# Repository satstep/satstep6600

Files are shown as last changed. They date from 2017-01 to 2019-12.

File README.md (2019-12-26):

<h1 style="font-family: courier;" align="center"> satstep6600</h1>
<p align="center">
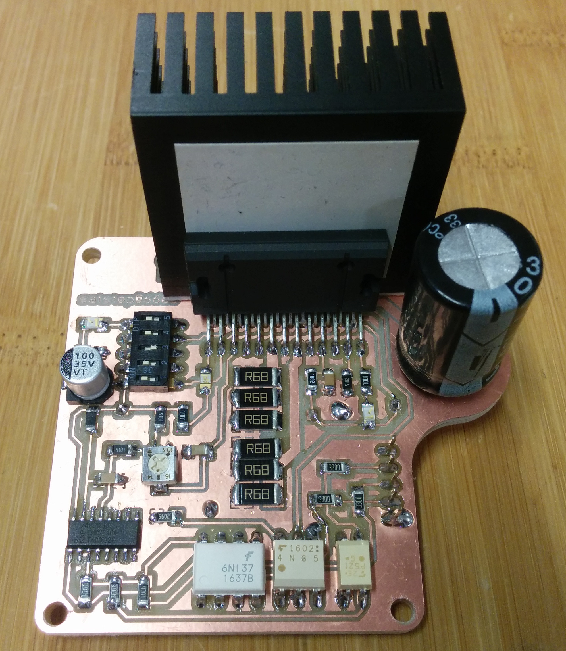
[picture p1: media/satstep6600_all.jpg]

<div align="center"><i>An open source & fabbable stepper driver based on TB6600.</i></div>
</p>

satstep6600
--

satstep6600 is a **low cost and fabbable** stepper driver. Inspired by the [PiBot TB6600 stepper driver](http://reprap.org/wiki/PiBot_TB6600_Stepper_Driver), satstep6600 is designed on purpose to maintain all the high power specs while being safe to be operated and easy to build, even using the stardard Fab Lab equipment.

satstep6600 features:

- chopper type stepper motor driver
- 5A peak output current, **4.5A** sustained maximum (over 2A a fan is recommended)
- 8-40V input voltage 
- 1/1, 1/2A(0-71-100%), 1/2B(0-100%), 1/4, 1/8, 1/16 stepping modes
- suitable for NEMA 17, NEMA 23 and few NEMA 34 stepper motors
- thermal shut down protection
- under voltage lock out protection
- over-current detection protection
- optoisolated for all the inputs
- 4 x M3 fixing holes
- board size of 70x63mm
- it costs **13 euro**

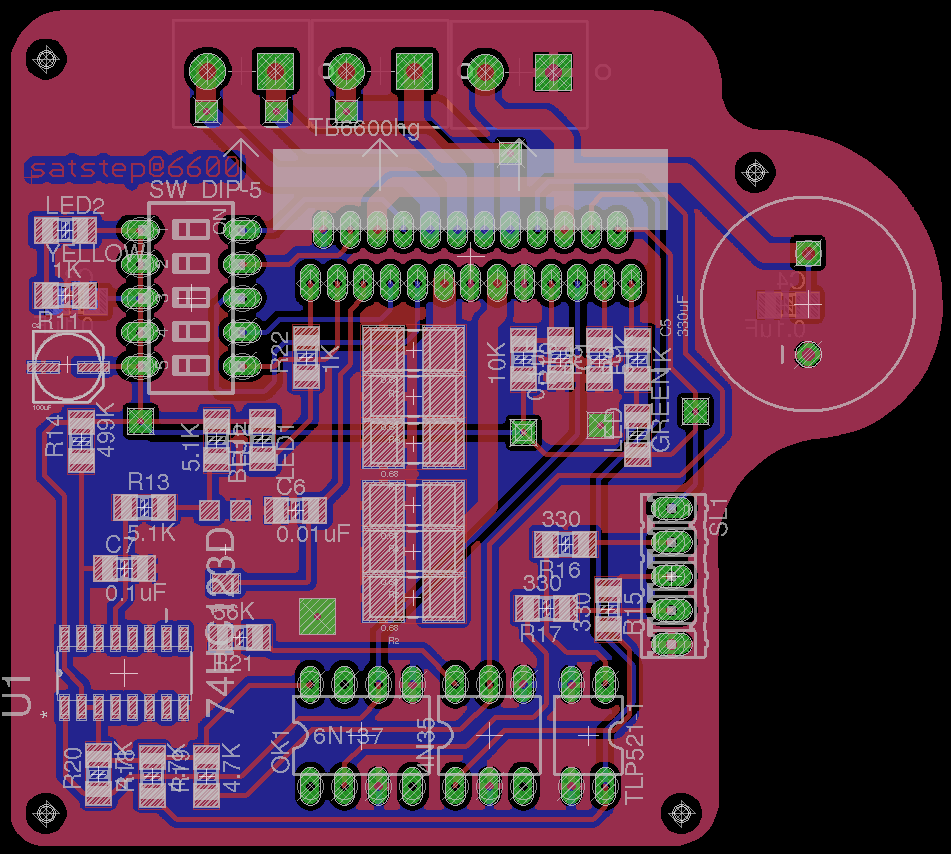
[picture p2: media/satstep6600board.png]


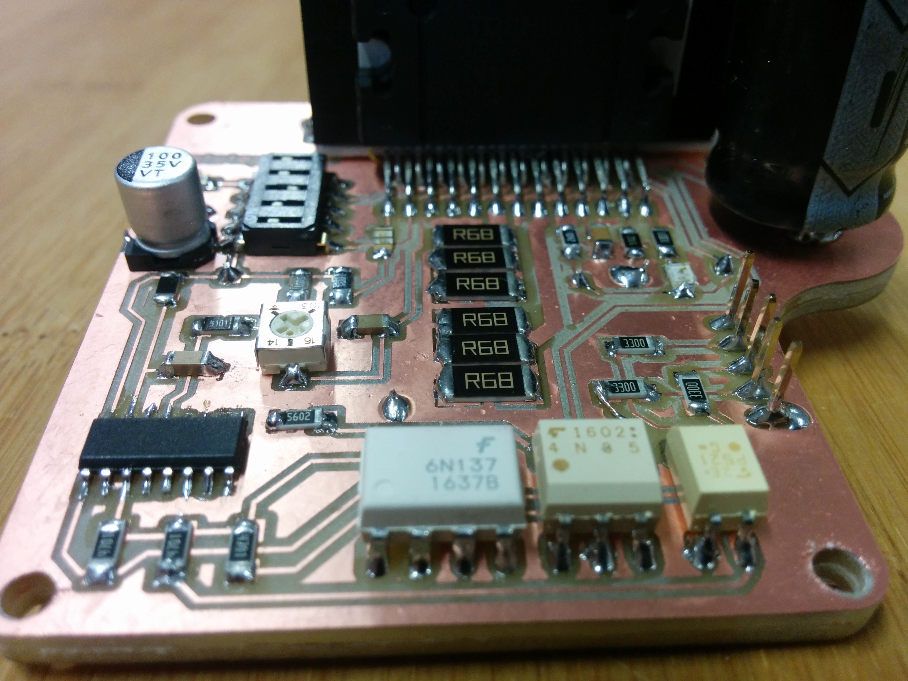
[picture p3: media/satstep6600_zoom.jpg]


Getting started
--

To connect your satstep6600 have a look to its **pinout**:

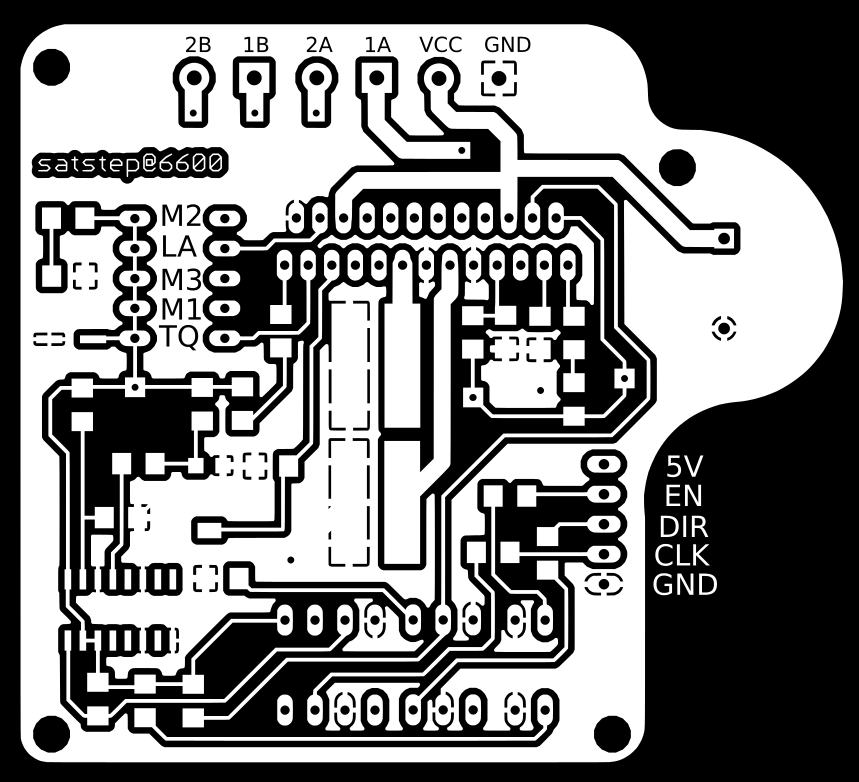
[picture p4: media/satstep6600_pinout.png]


and connect the pin as follows:

- **VCC** -> to the VCC of the power supply, supported voltage between 8-40V
- **GND** on top -> to the GND of the power supply
- **GND** on bottom right -> to the GND of your controller board (eg a [satshakit](https://github.com/satshakit/) or an Arduino)
- **DIR** -> to the direction pin of your controller board, this defines the direction of the rotation
- **CLK** -> to the CLK pin of your controller board, this is used to receive the signals to makes steps
- **EN** -> to a pin with digital signal of your controller board, LOW means ENABLED

To configure the driver you can use the 5 position dip switch and the trimmer. The trimmer will regulate the amount of current given to the motor. Please make sure that you will **never supply more current** than the amount in the datasheet of your stepper motor. **Rotating the trimmer towards 103 will increase the current.** For continous use over 2A is recommended to use a fan to cool down the driver. 

The dip swith will change other settings as the following list:
- **TQ on**: 100% input Vref, **TQ off**: 30% input Vref
- **LATCH on**: thermal shutdown and over current protection, **LATCH off**: only thermal shutdown
- **M1, M2, M3** define the stepping mode:
	- M1 off, M2 off, M3 off -> standby
	- M1 off, M2 off, M3 on -> 1/1
	- M1 off, M2 on, M3 off -> 1/2A (0-71-100%)
	- M1 off, M2 on, M3 on -> 1/2B
	- M1 on, M2 off, M3 off -> 1/4
	- M1 on, M2 off, M3 on -> 1/8
	- M1 on, M2 on, M3 off -> 1/16

Downloads
--

**downloads (right click, download as)**

- [satstep6600 board](https://github.com/satstep/satstep6600/raw/master/eagle/satstep6600.brd)
- [satstep6600 schematic](https://github.com/satstep/satstep6600/raw/master/eagle/satstep6600.sch)
- [satstep6600 top internal path png](https://github.com/satstep/satstep6600/raw/master/media/top_internal.png)
- [satstep6600 top external path png](https://github.com/satstep/satstep6600/raw/master/media/top_external.png)
- [satstep6600 bottom internal path png](https://github.com/satstep/satstep6600/raw/master/media/bottom_internal.png)
- [satstep6600 bottom external path png](https://github.com/satstep/satstep6600/raw/master/media/bottom_external.png)
- [satstep6600 board for 0.4 mills](https://github.com/satstep/satstep6600/raw/master/eagle/satstep6600_04/satstep6600.brd)
- [satstep6600 schematic for 0.4 mills](https://github.com/satstep/satstep6600/raw/master/eagle/satstep6600_04/satstep6600.sch)
- [satstep6600 for 0.4 mills top internal path png](https://github.com/satstep/satstep6600/raw/master/media/satstep6600_04/top_internal.png)
- [satstep6600 for 0.4 mills top external path png](https://github.com/satstep/satstep6600/raw/master/media/satstep6600_04/top_external.png)
- [satstep6600 for 0.4 mills bottom internal path png](https://github.com/satstep/satstep6600/raw/master/media/satstep6600_04/bottom_internal.png)
- [satstep6600 for 0.4 mills bottom external path png](https://github.com/satstep/satstep6600/raw/master/media/satstep6600_04/bottom_external.png)
- [satstep6600 BOM ods](https://github.com/satstep/satstep6600/raw/master/docs/satstep6600_BOM.ods)
- [satstep6600 BOM xlsx](https://github.com/satstep/satstep6600/raw/master/docs/satstep6600_BOM.xlsx)

Media
--

videos of satstep6600 moving NEMA 23 stepper motors:

<a href="http://www.youtube.com/watch?feature=player_embedded&v=5523ECHDnfE
" target="_blank"></a>

<a href="http://www.youtube.com/watch?feature=player_embedded&v=U822JZaIcNg
" target="_blank"></a>

other images of the satstep6600 driver board:

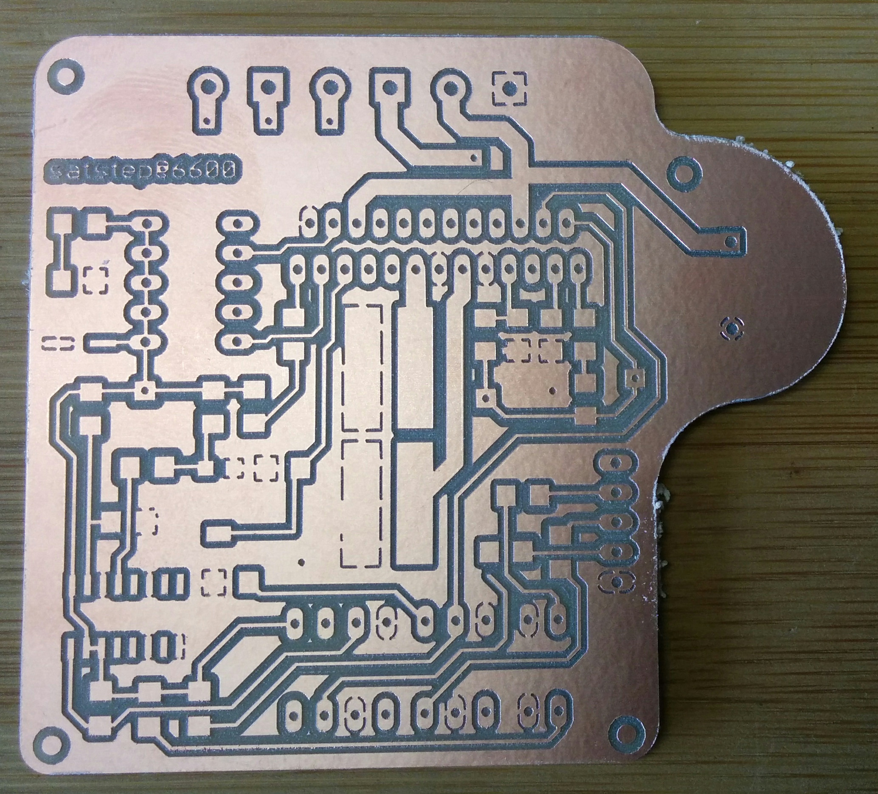
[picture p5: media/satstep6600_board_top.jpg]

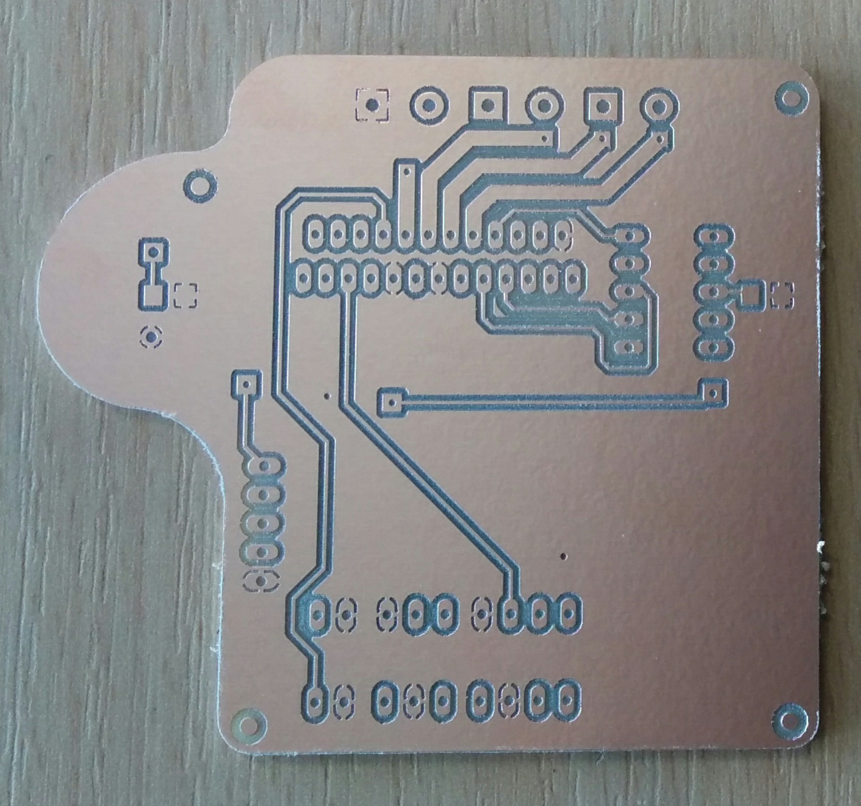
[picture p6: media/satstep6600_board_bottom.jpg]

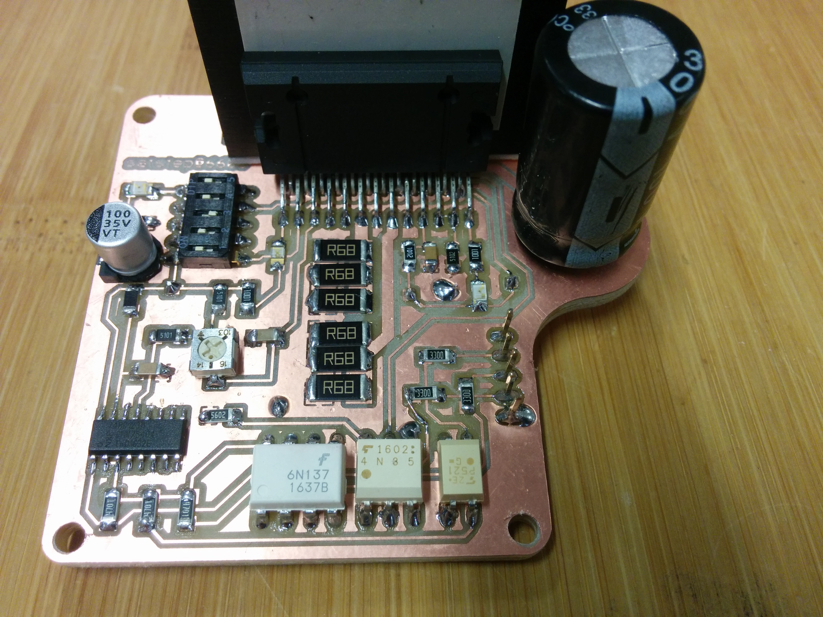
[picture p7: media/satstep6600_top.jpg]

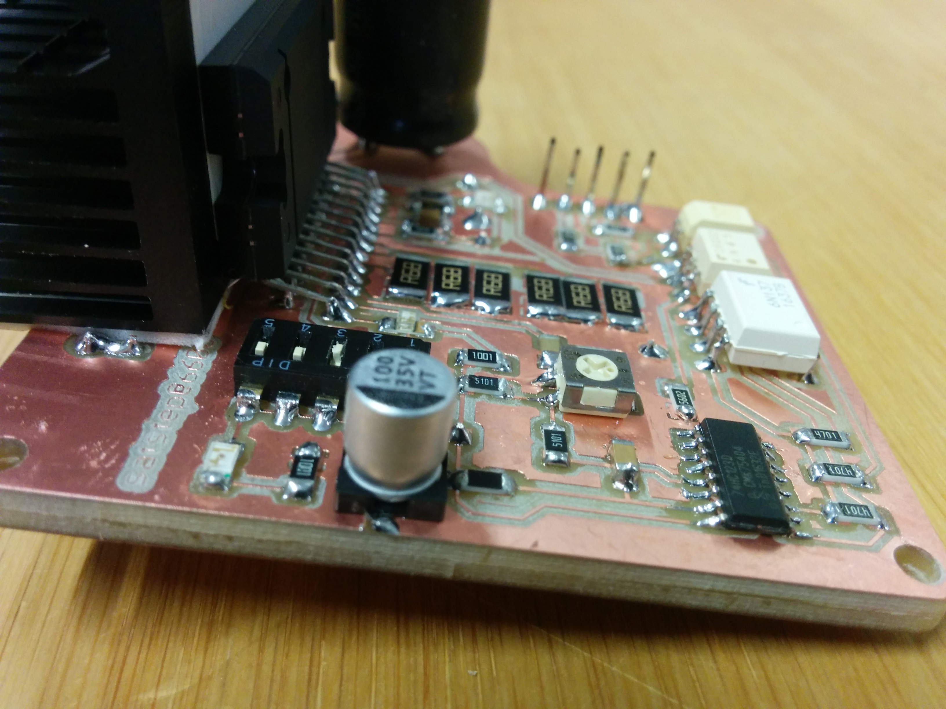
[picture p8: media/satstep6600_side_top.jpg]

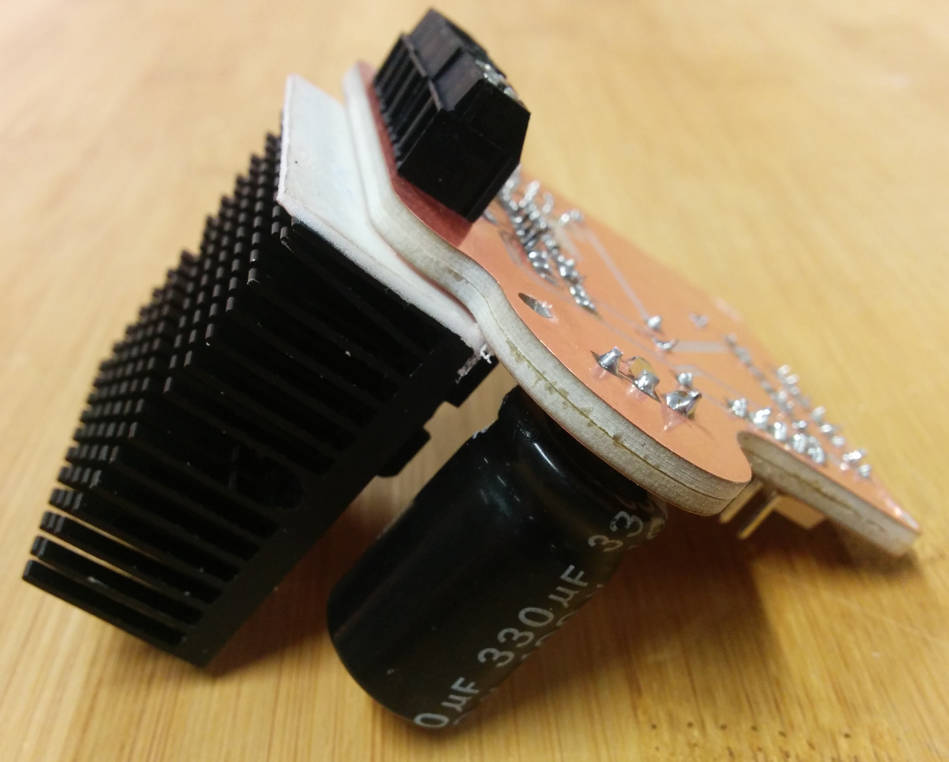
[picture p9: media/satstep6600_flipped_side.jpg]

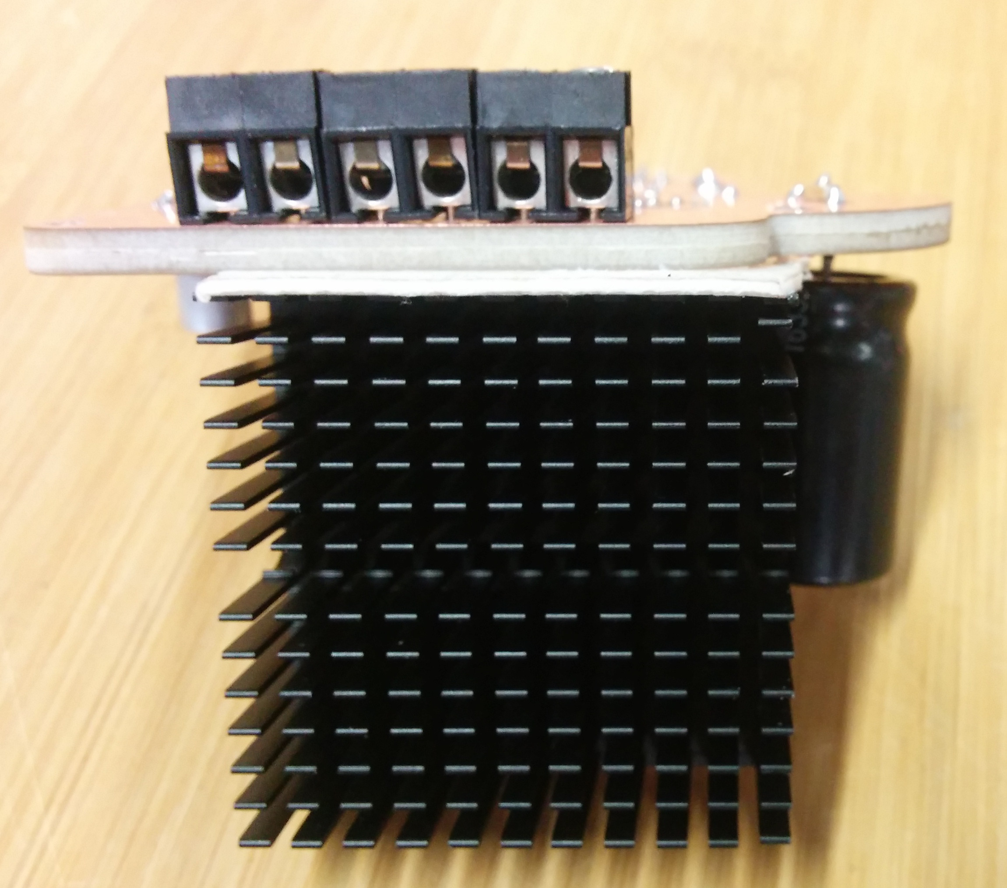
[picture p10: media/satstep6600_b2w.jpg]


What's in the repo
--

- **[docs](https://github.com/satstep/satstep6600/tree/master/docs)**: BOM files
- **[egle](https://github.com/satstep/satstep6600/tree/master/eagle)**: eagle projects of the satstep6600 drive
- **[media](https://github.com/satstep/satstep6600/tree/master/media)**: svgs, connections schemas, images for cnc milling machine, other images

Authors
--

- Daniele Ingrassia

Contact
--

- **ingrassiada@gmail.com**
- **[linkedin](http://it.linkedin.com/in/danieleingrassia)**

Thanks
--

[Fablab Kamp-Lintfort](http://fablab.hochschule-rhein-waal.de/index.php/de/)<br />
Hochschule Rhein-Waal<br />
Friedrich-Heinrich-Allee 25, 47475 Kamp-Lintfort, Germany<br />
fablab@hochschule-rhein-waal.de

License
--

This work is licensed under the terms of the open source license: Creative Commons Attribution-ShareAlike 4.0 International ([CC BY-SA 4.0](https://creativecommons.org/licenses/by-sa/4.0/)).

Disclaimer  
--

<div class="align-justify">
This hardware/software is provided "as is", and you use the hardware/software at your own risk. Under no circumstances shall any author be liable for direct, indirect, special, incidental, or consequential damages resulting from the use, misuse, or inability to use this hardware/software, even if the authors have been advised of the possibility of such damages.</div>

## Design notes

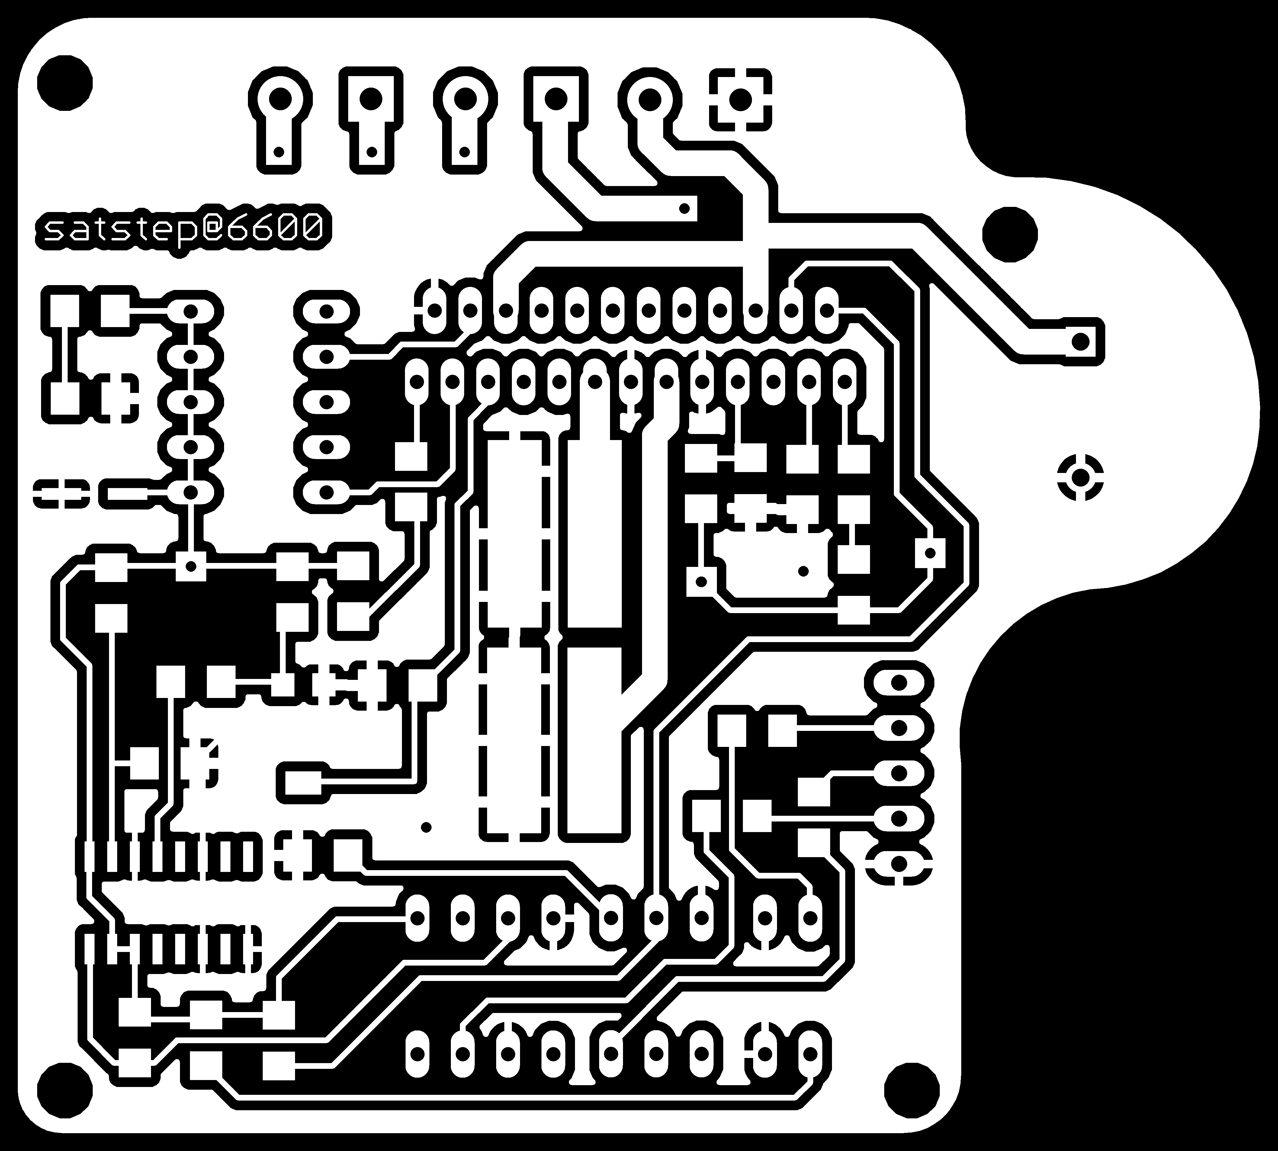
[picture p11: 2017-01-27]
media/satstep6600_04/top_internal.png

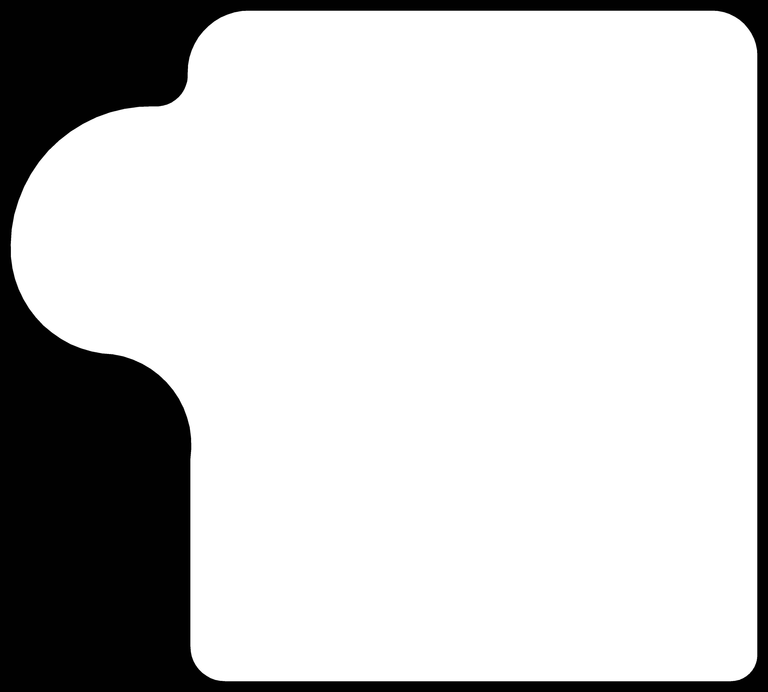
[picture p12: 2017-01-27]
media/bottom_external.png

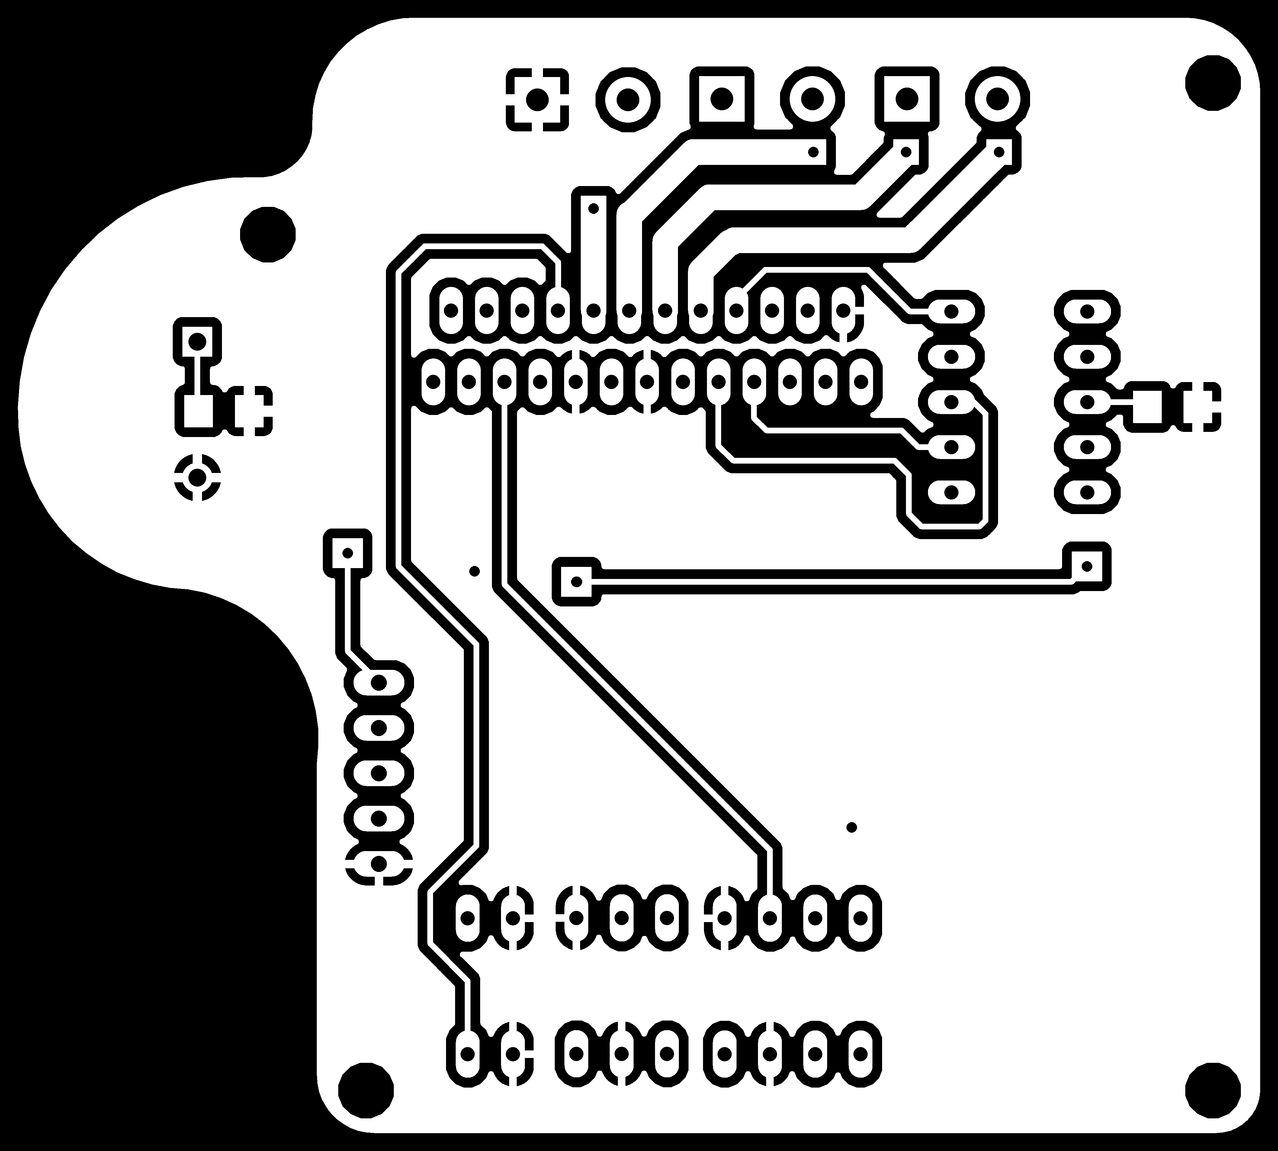
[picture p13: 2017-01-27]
media/satstep6600_04/bottom_internal.png

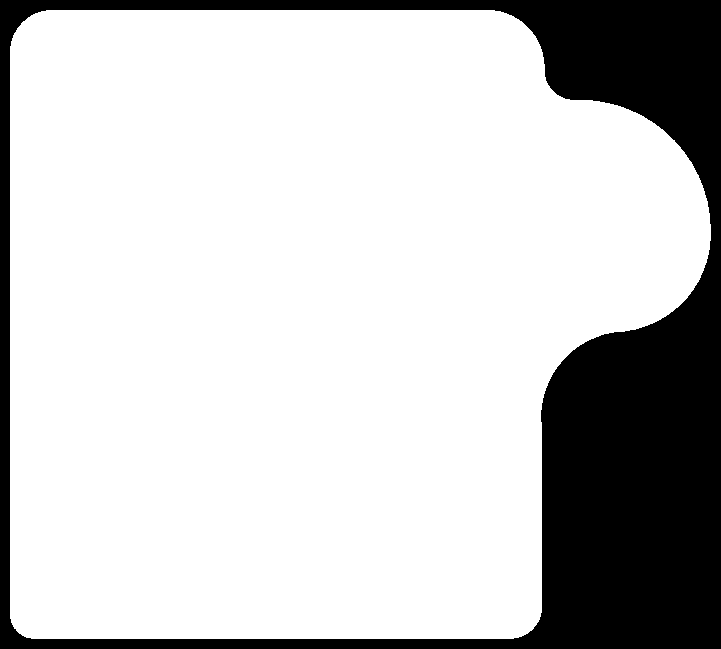
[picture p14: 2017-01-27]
media/top_external.png

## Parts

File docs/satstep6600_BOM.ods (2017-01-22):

Value | Manufacturer Part No | Package | Description | Link | Price € | Quantity | Total price
- | Toshiba TB6600HG | HZIP25-P-1.00F | stepper driver IC | aliexpress (https://www.aliexpress.com/item/2pcs-lot-new-original-TB6600HG-stepper-motor-driver-chip-ZIP25-package/32770866573.html) | 3.50 | 1 | 3.50
- | 74HC123D | SOIC 16 pin | monostable multivibrator | 1085332 (http://de.farnell.com/nxp/74hc123d/74hc-cmos-smd-74hc123-soic16/dp/1085332?CMP=i-ddd7-00001003) | 0.42 | 1 | 1.00
5.1K | WCR1206-5K1FI | 1206 | smd resistor | 1100211 (http://de.farnell.com/welwyn/wcr1206-5k1fi/dickschichtwiderstand-5k1-1-0/dp/1100211?CMP=i-ddd7-00001003) | 0.03 | 2 | 0.06
51K | WCR1206-51KFI | 1206 | smd resistor | 1100237 (http://de.farnell.com/welwyn/wcr1206-51kfi/dickschichtwiderstand-51k-1-0/dp/1100237?CMP=i-ddd7-00001003) | 0.03 | 1 | 0.29
24A | PM5.08/2/90 BLK | 5.08 | wire to board | 1131855 (http://de.farnell.com/weidmuller/pm5-08-2-90-blk/anschlussblock-side-entry-2polig/dp/1131855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) | 0.52 | 3 | 1.56
10K | TS53YL103MR10 | - | trimmer potentiometer | 1141474 (http://de.farnell.com/vishay/ts53yl103mr10/trimmpotentiometer-10k-1-gang/dp/1141474?CMP=i-ddd7-00001003) | 1.15 | 1 | 1.15
2.5KV | 4N35 | DIP 6 pin | optocoupler | 1523998 (http://de.farnell.com/vishay/4n35/optokoppler-fototransistor-5000vrms/dp/1328375?CMP=i-ddd7-00001003) | 0.33 | 1 | 0.33
5 switches | MCEIR-05 | DIP 10 pin | DIP switch | 1328375 (http://de.farnell.com/multicomp/mceir-05/schalter-dil-5polig/dp/1523998?CMP=i-ddd7-00001003) | 0.48 | 1 | 0.48
yellow | MCL-S250YC | 1206 | smd led | 1581231 (http://de.farnell.com/multicomp/mcl-s250yc/led-smd-1206-gelb/dp/1581231?CMP=i-ddd7-00001003) | 0.24 | 1 | 0.24
green | MCL-S250GC | 1206 | smd led | 1581232 (http://de.farnell.com/multicomp/mcl-s250gc/led-smd-1206-gr-n/dp/1581232?CMP=i-ddd7-00001003) | 0.21 | 1 | 0.21
10nF | MC1206B103K500CT | 1206 | smd capacitor | 1759350 (http://de.farnell.com/multicomp/mc1206b103k500ct/kondensator-mlcc-x7r-10nf-50v/dp/1759350?CMP=i-ddd7-00001003) | 0.04 | 1 | 0.04
100nF | MC1206B104K101CT | 1206 | smd capacitor | 1759366 (http://de.farnell.com/multicomp/mc1206b104k101ct/kondensator-mlcc-x7r-100nf-100v/dp/1759366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) | 0.05 | 4 | 0.19
8.2 °C/W | BGA-STD-115 | 18-40-40 | heatsink | 2084448 (http://de.farnell.com/abl-heatsinks/bga-std-115/bga-k-hlk-rper-standard-8-2-c/dp/2084448?CMP=i-ddd7-00001003) | 1.92 | 1 | 1.92
0.68 | - | 2512 | smd resistor | aliexpress (https://www.aliexpress.com/item/50-pcs-2512-SMD-Resistor-1W-0-68R-1-Chip-Resistor/32509428965.html) | 0.029 | 6 | 0.17
10K | MCWR12X1002FTL | 1206 | smd resistor | 2447455 (http://de.farnell.com/multicomp/mcwr12x1002ftl/dickschichtwiderstand-10kohm-1/dp/2447455?CMP=i-ddd7-00001003) | 0.01 | 1 | 0.01
1K | MCWR12X1001FTL | 1206 | smd resistor | 2447473 (http://de.farnell.com/multicomp/mcwr12x1001ftl/dickschichtwiderstand-1k-1-0-25w/dp/2447473?CMP=i-ddd7-00001003) | 0.01 | 3 | 0.03
330 | MCWR12X3300FTL | 1206 | smd resistor | 2447504 (http://de.farnell.com/multicomp/mcwr12x3300ftl/dickschichtwiderstand-330r-1-0/dp/2447504?CMP=i-ddd7-00001003) | 0.01 | 3 | 0.03
4.7K | MCWR12X4701FTL | 1206 | smd resistor | 2447523 (http://de.farnell.com/multicomp/mcwr12x4701ftl/dickschichtwiderstand-4k7-1-0/dp/2447523?CMP=i-ddd7-00001003) | 0.01 | 3 | 0.04
56K | MCWR12X5602FTL | 1206 | smd resistor | 2447528 (http://de.farnell.com/multicomp/mcwr12x5602ftl/dickschichtwiderstand-56kohm-1/dp/2447528?CMP=i-ddd7-00001003) | 0.01 | 2 | 0.01
- | 6N137 | DIP 8 pin | optocoupler | aliexpress (https://www.aliexpress.com/item/10PCS-6N137-DIP8-ISOLATOR-2-5KVRMS-1CH-OPEN-NEW-GOOD-QUALITY/32674496188.html) | 0.15 | 1 | 0.15
330uF | MCKSK100M331J26S | DIP | through hole capacitor | 2610809 (http://de.farnell.com/multicomp/mcksk100m331j26s/kondensator-alu-elko-330uf-100v/dp/2610809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) | 0.77 | 1 | 0.77
100uF | MCVVT035M101EA6L | - | smd capacitor | 2611381 (http://de.farnell.com/multicomp/mcvvt035m101ea6l/kond-alu-elko-100uf-35v-becher/dp/2611381?CMP=i-ddd7-00001003) | 0.16 | 1 | 0.16
2.5KV | TLP521-1 | DIP 4 pin | optocoupler | aliexpress (https://www.aliexpress.com/item/Line-in-TLP521-1-P521-1-Integrated-Transistor-Output-DIP-4-20-pcs/32764570714.html) | 0.10 | 1 | 0.10
499K | MC0125W12061499K | 1206 | smd resistor | 2142323 (http://de.farnell.com/multicomp/mc0125w12061499k/dickschichtwiderst-499k-1-0-125w/dp/2142323) | 0.00 | 1 | 0.03
red | MCL-S250SRC | 1206 | smd led | 1581229 (http://de.farnell.com/multicomp/mcl-s250src/led-smd-1206-super-rot-markierung/dp/1581229) | 0.15 | 1 | 0.15
- | - | 0.1” | pin headers | ebay (http://www.ebay.de/itm/161710783850) | 0.39 | 1 | 0.39
 |  |  |  |  |  |  | Total price:
 |  |  |  |  |  |  | 13.01

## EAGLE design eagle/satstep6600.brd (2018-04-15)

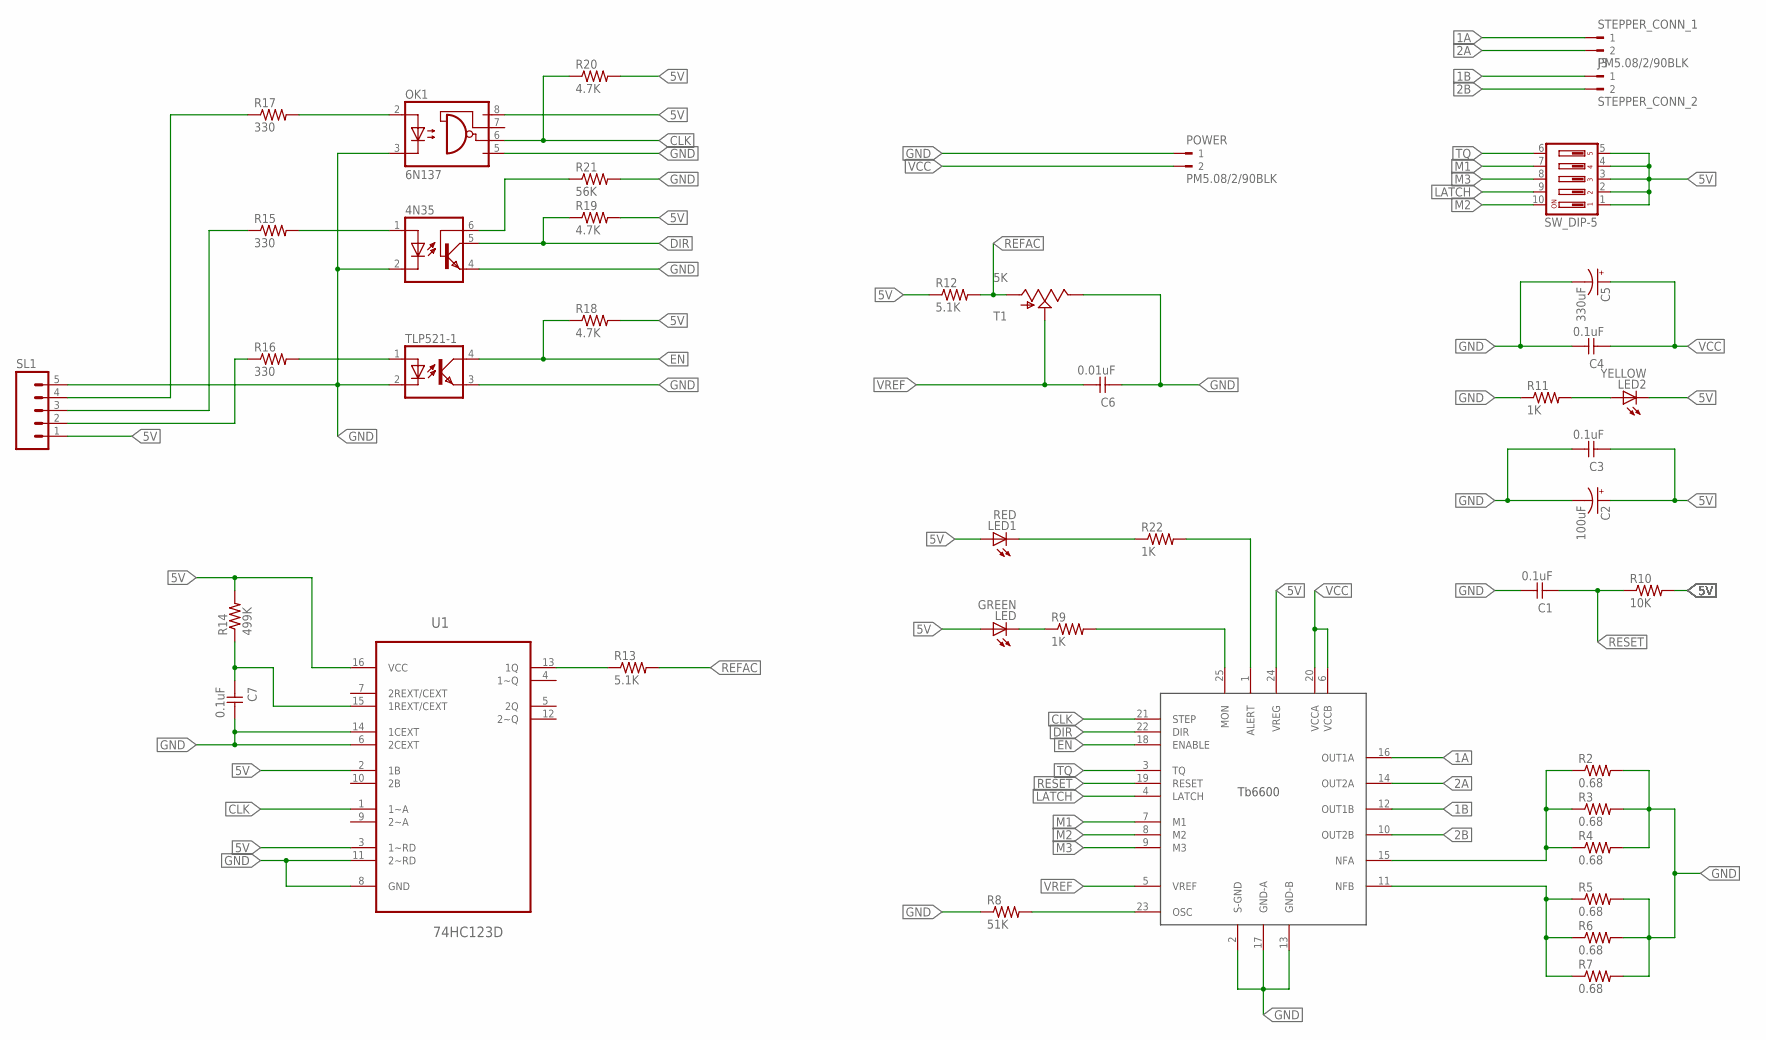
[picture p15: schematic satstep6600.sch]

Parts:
4N35: 4N35; DIL06
C1, C3, C4, C7: 0.1uF; 1206
C2: 100uF; PANASONIC_C
C5: 330uF; CPOL-RADIAL-1000UF-63V
C6: 0.01uF; 1206
J3: STEPPER_CONN_2; WEIDMULLER_PM5.08_2
LED: GREEN; 1206
LED1: RED; 1206
LED2: YELLOW; 1206
OK1: 6N137; DIL08
POWER: PM5.08/2/90BLK; WEIDMULLER_PM5.08_2
R2, R3, R4, R5, R6, R7: 0.68; 2512
R8: 51K; R1206
R9, R11, R22: 1K; R1206
R10: 10K; R1206
R12, R13: 5.1K; R1206
R14: 499K; R1206
R15, R16, R17: 330; R1206
R18, R19, R20: 4.7K; R1206
R21: 56K; R1206
SL1: M05; 05P
STEPPER_CONN_1: PM5.08/2/90BLK; WEIDMULLER_PM5.08_2
SW_DIP-5: SD4-05
T1: 5K; TS53YL104MR10_TRIMMER
TLP521-1: PC817; DIL04
U1: 74HC123D; SOIC127P600X175-16N
U$1: TB6600HG; P-HZIP25-1.00G

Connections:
1A: STEPPER_CONN_1.1, U$1.16 (OUT1A)
1B: J3.1, U$1.12 (OUT1B)
2A: STEPPER_CONN_1.2, U$1.14 (OUT2A)
2B: J3.2, U$1.10 (OUT2B)
5V: C2.+, C3.1, LED.1 (A), LED1.1 (A), LED2.2 (C), OK1.8 (VCC), R10.2, R12.1, R14.2, R18.2, R19.2, R20.2, SL1.1, SW_DIP-5.1, SW_DIP-5.2, SW_DIP-5.3, SW_DIP-5.4, SW_DIP-5.5, U1.2 (1B), U1.3 (1~RD), U1.16 (VCC), U$1.24 (VREG)
ALERT: R22.2, U$1.1 (ALERT)
CLK: OK1.6 (VO), R20.1, U1.1 (1~A), U$1.21 (STEP)
DIR: 4N35.5 (COL), R19.1, U$1.22 (DIR)
EN: R18.1, TLP521-1.4 (COL), U$1.18 (ENABLE)
GND: 4N35.2 (C), 4N35.4 (EMI), C1.2, C2.-, C3.2, C4.2, C5.2 (-), C6.1, C7.2, OK1.3 (C), OK1.5 (GND), POWER.1, R2.2, R3.2, R4.2, R5.2, R6.2, R7.2, R8.1, R11.1, R21.2, SL1.5, T1.P$2 (E), TLP521-1.2 (C), TLP521-1.3 (EMIT), U1.6 (2CEXT), U1.8 (GND), U1.11 (2~RD), U1.14 (1CEXT), U$1.2 (S-GND), U$1.13 (GND-B), U$1.17 (GND-A)
LATCH: SW_DIP-5.9, U$1.4 (LATCH)
M1: SW_DIP-5.7, U$1.7 (M1)
M2: SW_DIP-5.10, U$1.8 (M2)
M3: SW_DIP-5.8, U$1.9 (M3)
unnamed: R5.1, R6.1, R7.1, U$1.11 (NFB)
unnamed: R8.2, U$1.23 (OSC)
unnamed: LED.2 (C), R9.1
unnamed: R2.1, R3.1, R4.1, U$1.15 (NFA)
unnamed: LED1.2 (C), R22.1
unnamed: LED2.1 (A), R11.2
unnamed: R13.1, U1.13 (1Q)
unnamed: C7.1, R14.1, U1.15 (1REXT/CEXT)
unnamed: R16.2, TLP521-1.1 (A)
unnamed: 4N35.1 (A), R15.2
unnamed: OK1.2 (A), R17.2
unnamed: 4N35.6 (BAS), R21.1
unnamed: R16.1, SL1.2
unnamed: R15.1, SL1.3
unnamed: R17.1, SL1.4
unnamed: R9.2, U$1.25 (MON)
REFAC: R12.2, R13.2, T1.P$3 (A)
RESET: C1.1, R10.1, U$1.19 (RESET)
TQ: SW_DIP-5.6, U$1.3 (TQ)
VCC: C4.1, C5.1 (+), POWER.2, U$1.6 (VCCB), U$1.20 (VCCA)
VREF: C6.2, T1.P$1 (S), U$1.5 (VREF)

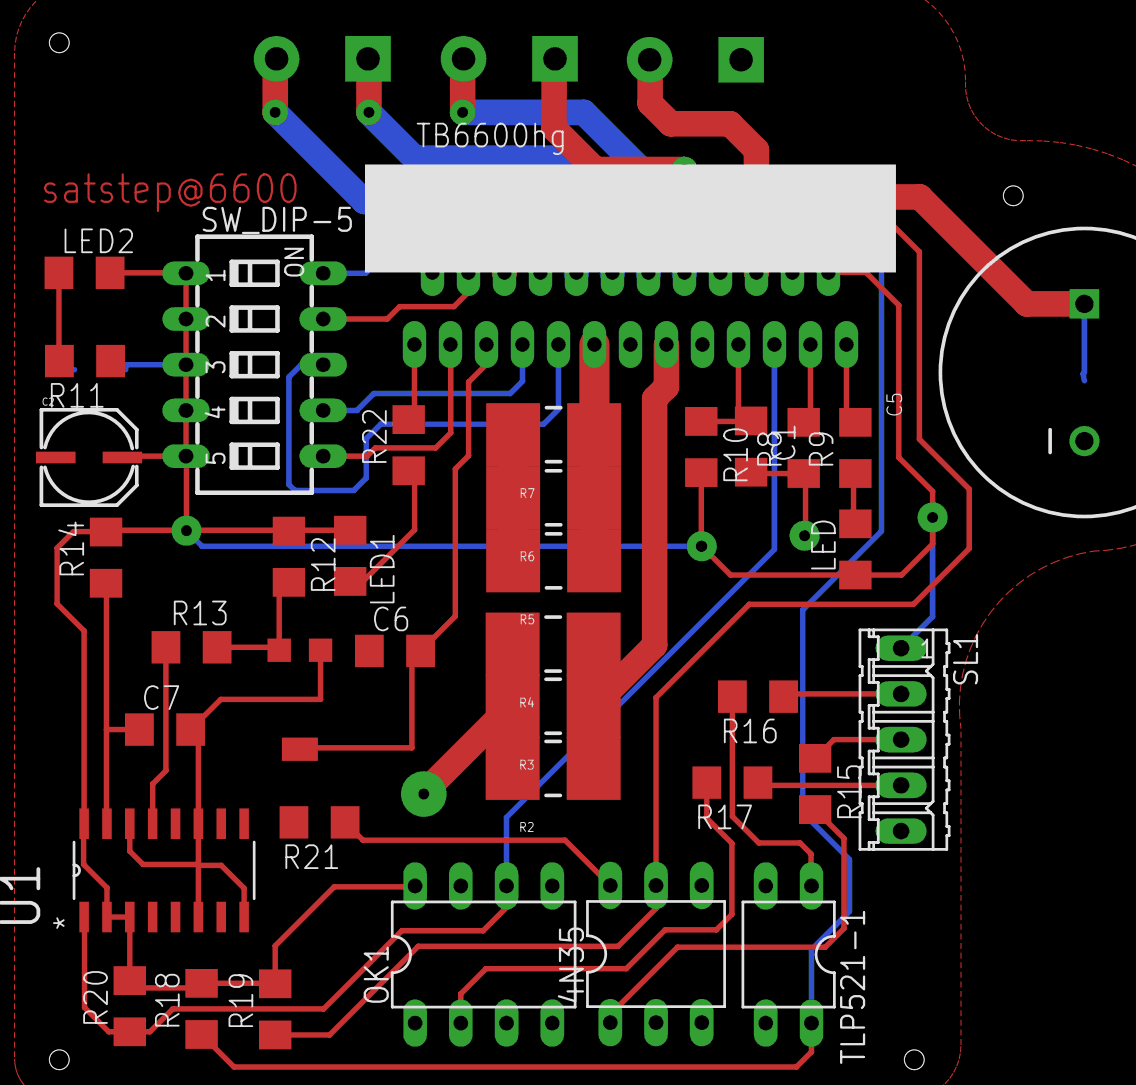
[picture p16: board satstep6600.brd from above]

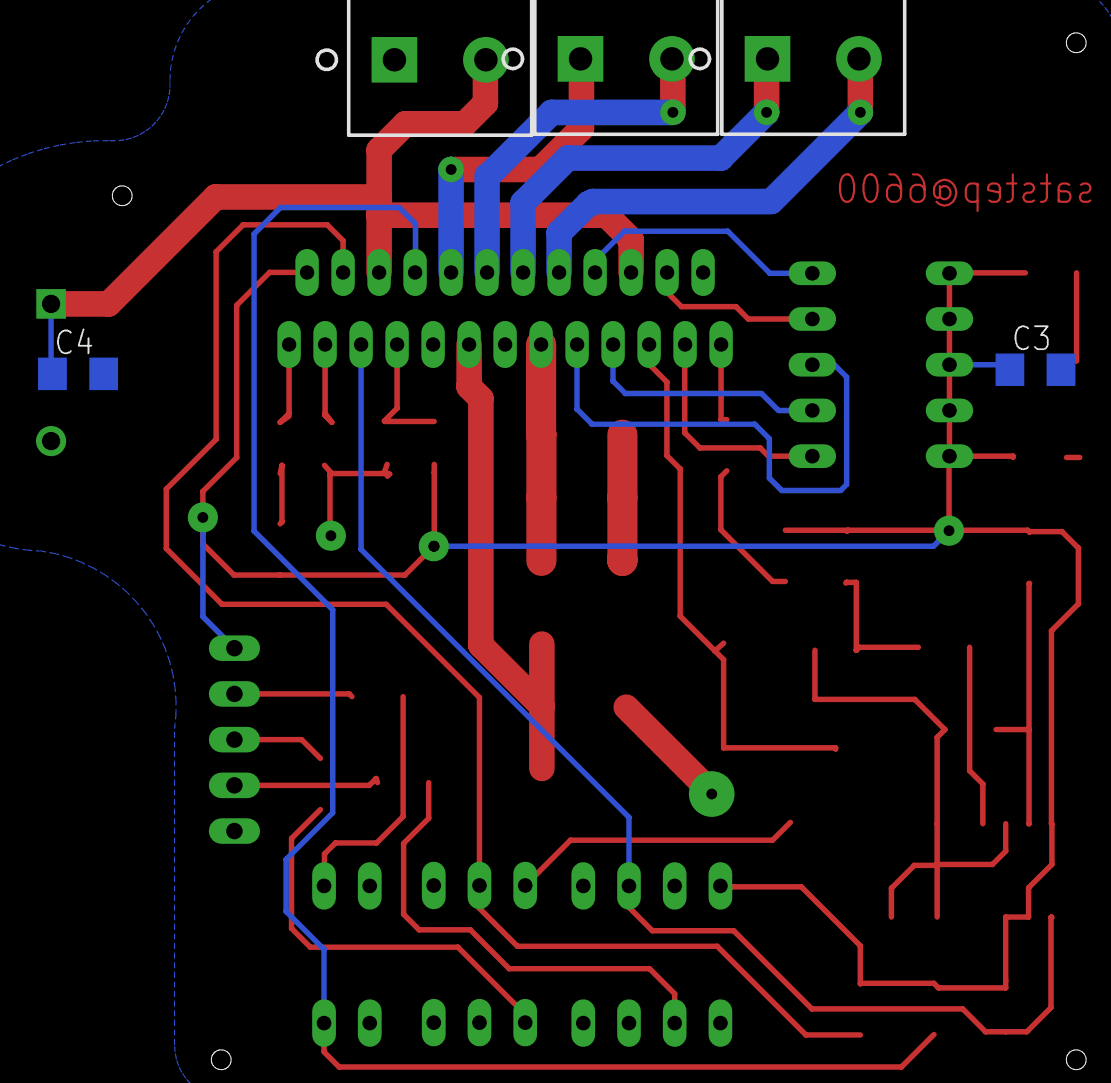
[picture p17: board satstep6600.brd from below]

Board: 2 copper layers, 42 parts (5 on the bottom side), 35 nets.

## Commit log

2017-01-22 added eagle files and images of the pcbs
    [driver_tb6600.brd, driver_tb6600.sch]
2017-01-22 added BOM
    [satstep6600_BOM.ods, satstep6600_BOM.xlsx]
2017-01-24 renamed eagle files according to the given name of the driver
    [satstep6600.brd, satstep6600.sch]
2017-01-24 added recommendation on the fan
2017-01-27 added new version for 0.4mm mills and resized all the pngs
2018-04-15 mod the trimmmer value
    [satstep6600.brd, satstep6600.sch]
2018-04-15 safier trimmer value
    [satstep6600.brd, satstep6600.sch]
2018-04-15 safer trimmer value
    [satstep6600.brd, satstep6600.sch]

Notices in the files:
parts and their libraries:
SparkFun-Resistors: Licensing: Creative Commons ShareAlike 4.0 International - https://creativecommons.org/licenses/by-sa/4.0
